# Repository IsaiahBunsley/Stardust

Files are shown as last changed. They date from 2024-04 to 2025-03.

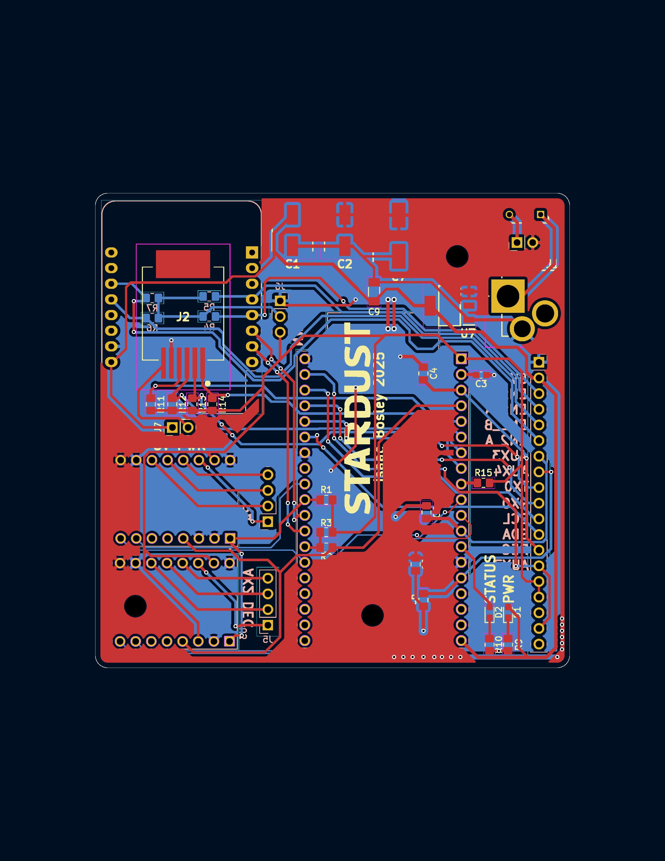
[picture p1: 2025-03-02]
Images/CircuitBoard-page-001 (1).jpg

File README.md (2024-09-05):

# Stardust
Harmonic gear driven equatorial mount for astrophotography.

GOALS:
 - Achieve sub arcsecond prescision
 - Make a sleek and nice-to-view body assembly
 - Use as few pre-made assemblies as possible
 - Ample wieght capacity ( >10 lbs, ideally >20 lbs )
 - Ease of use/control using pre-developed software such as PHD2, OnStep, etc...
 - Design a PCB to house stepper controllers, microcrontroller, WiFi, etc..
 - Efficient homing process
 - Create a product that is not only good-looking but easy to use and enjoy

NOTES:
V1 Is way to large and clunky

Using a 100:1 harmonic and a ~3.33:1 pulley system we can achieve sub arcsecond tracking using 256 microstepping and approx 20 arcsecond tracking with no microstepping. UPDATE: Using a 0.9deg stepper 10 arcsecond (per step)
can be had. A 0.9deg stepper with 1/16 microstepping will give us 0.6 arcseconds per step. This will have to be used to meet design requiremetns as well as to avoid microstepping as it can lead to error.

M3 bolts were used on bolting the body together. If this does not prove to be rigid enough more bolts can be added or a redesign including angle brackets will be needed.

Clearances with the stepper motors are extremely tight. If NEMA 17 motors will not work it would be OK to swap the DEC axis for a smaller NEMA 14 stepper.

Product IDs for the gears are given but expensive. If suitable replacements with similar specs can be found it would be OK to swap. Same with belts. The only issue would be lack of 
quality control from other sources (Amazon...). Cheaping out on a $20 belt would introduce backlash and tracking errors to the ~$1000 harmonic drives.

The angle brackets used to mount the steppers are called out as 6061 alum alloy but could possibly be 3d printed or bought from Mcmaster Carr if a similar design was found.

A redesign of the tangent mount is needed. This tangent mount is made by William Optics and could be fitted into the design for $250: https://williamoptics.com/products/wo-vixen-style-latitude-base-mount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

After looking through the new AM5N's product specs the following seems true:
reduction ratio: 300:1 
         This means that they are using a 100:1 HD paired with a 3:1 belt. With this setup they are claiming a arcsec/step of 0.17. This means that they are using stepper microstepping of 1/64 (0.9 / 300 / 64 = deg -> 0.1687 arcseconds) (also assuming 0.9deg steppers).
There is also a claimed "high payload" mode. I believe that this "mode" simply changes the microstepping value to something more reasonable such as 1/16. This will increase the availiable current per step and thus give more reliable tracking (less periodic error) where more current per step is needed (higher payloads).

DESIGN IDEAS:
For implementing a homing process - Use a arm that mounts to the main axis (axe-eees) that goes down the length of the HD and will pass over some sort of magnetic sensor or inductive position
sensor. This will allow the motors to spin the HD until a sensor detects an object meaning the output shaft of the HD is in the correct location.

Add an encoder and brake to the stepper shaft. 

Allow for EQ mode OR an alt/az mode (by removing the tangent assembly).

INSPIRATION:
Alkaid by JZ - https://github.com/alanzjl/AlkaidMount
ZWO AM5 - https://www.highpointscientific.com/zwo-am5n-harmonic-drive-equatorial-mount-with-tripod
William Optics Latitude Base - https://williamoptics.com/products/wo-vixen-style-latitude-base-mount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

0.9 Stepper - https://www.moonsindustries.com/p/nema-17-high-precision-hybrid-stepper-motors/ms17ha4p4040-000004611110015909
ONSTEP      - https://onstep.groups.io/g/main/wiki/4414

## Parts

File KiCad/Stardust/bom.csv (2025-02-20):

Id | Designator | Footprint | Quantity | Designation | Supplier and ref
1 | C6,C5,C8,C4 | C_2220_5750Metric_Pad1.97x5.40mm_HandSolder | 4 | 100nF
2 | R1,R3,R9,R10,R6,R5,R4,R7 | R_0805_2012Metric_Pad1.20x1.40mm_HandSolder | 8 | 4.7K
3 | D2 | LED_0603_1608Metric_Pad1.05x0.95mm_HandSolder | 1 | STATUS LED
4 | J7,J3 | PinHeader_1x02_P2.54mm_Vertical | 2 | 1x2 Connector
5 | J2 | RJ12_855135114 | 1 | RJ12
6 | R14,R15,R13,R12,R11 | R_0805_2012Metric_Pad1.20x1.40mm_HandSolder | 5 | 2.4K
7 | U8 | FuseHolder_RHDR2W53P0X508_1X2 | 1 | LittlFuse 2.5 Amp
8 | G1,G1 | logo_footprint | 2 | LOGO
9 | C7 | 100uFElectrolyticCap_CAPAE830X1080N | 1 | 100 uF
10 | U7 | 5VREG_SOT230P700X180-4N | 1 | Regulator - 5V 1A
11 | C2,C1 | 10uFElectrolyticCap_CAPAE660X550N | 2 | 10 uF
12 | D1 | LED_0603_1608Metric_Pad1.05x0.95mm_HandSolder | 1 | PWR LED
13 | C3 | C_0603_1608Metric_Pad1.08x0.95mm_HandSolder | 1 | 10uF
14 | C9 | C_1206_3216Metric_Pad1.33x1.80mm_HandSolder | 1 | 330nF
15 | R2 | R_0805_2012Metric_Pad1.20x1.40mm_HandSolder | 1 | 1K
16 | J1 | DC_PowerConn_694108402002 | 1 | 12V DC
17 | U2,U3 | MODULE_TMC2209_SILENTSTEPSTICK | 2 | BTT TMC2209 V1.3
18 | U1 | MODULE_ESP32-DEVKITC | 1 | ESP32
19 | J5,J4 | PinHeader_1x04_P2.54mm_Vertical | 2 | Conn_01x04_Pin
20 | J6 | PinHeader_1x03_P2.54mm_Vertical | 1 | 1x3 Header
21 | J8 | PinHeader_1x19_P2.54mm_Vertical | 1 | Conn_01x19_Pin
22 | U4 | WEMOS_D1_mini_light | 1 | WEMOS_D1_mini

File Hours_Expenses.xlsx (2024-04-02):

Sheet: Hours
Date | Hours | Total Days | Total Hours
2024-03-21 | 8 | 0.50 | 12
2024-03-22 | 4

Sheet: Expenses
Item | Cost per Item | Shipping | Taxes | Quantity | Total | Total Spent
CSF-17-100-2UH Harmonic Drive | $210.00 | $8.00 | $28.89 | 2 | $456.89 | $456.89

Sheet: Sheet1
Part Number | Item Name | Manufacturer | Cost | Comment
60-2P06MDFP8 | GT2 Timing Belt Pulley 18 Tooth | B&B Manufacturing | $18.20 | B&B Items do not have CAD files so cannot test fitment
GPA18GT2060-A-H5 | GT2 Timing Belt Pulley 18 Tooth | MISUMI | $18.10
18-2P06M6FA5 | GT2 Timing Belt Pulley 60 Tooth | B&B Manufacturing | $7.63 | B&B Items do not have CAD files so cannot test fitment
GPA60GT2060-A-H8 | GT2 Timing Belt Pulley 60 Tooth | MISUMI | $28.32
144-2P-06 | GT2 Belt 144mm | B&B Manufacturing | $6.34 | B&B Items do not have CAD files so cannot test fitment
GBN1442GT-60 | GT2 Belt 144mm | MISUMI | $6.50
DW-AD-601-M8-121 | Inductive Position Sensor | Contrinex | $17.00
59060-1-T-03-A | Inductive Position Sensor | Littelfuse | $9.83
 |  |  | $64.46

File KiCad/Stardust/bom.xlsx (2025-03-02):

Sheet: bom
Mouser/DigiKey PN | MFR PN | Quantity | Price | Total | Mouser | Digikey | Amazon | Ordered?
710-865230643009 | 865230643009 | 2 | $0.26 | $0.52 | y |  |  | y
810-C1608X7T1A106M08 | C1608X7T1A106M080AC | 1 | $0.23 | $0.23 | y |  |  | y
581-KAM21BR71H104JT | KAM21BR71H104JT | 4 | $0.32 | $1.28 | y |  |  | y
647-GXC1V101MCQ1GS | GXC1V101MCQ1GS | 1 | $1.78 | $1.78 | y |  |  | y
581-KAM31NR81H334KU | KAM31NR81H334KU | 1 | $0.49 | $0.49 | y |  |  | y
720-P4112S2U1252X4X5 | KT EELP41.12-S2U1-25-2X4X-5-R18 | 2 | $0.30 | $0.60 | y |  |  | y
710-694108402002 | 694108402002 | 1 | $1.21 | $1.21 | y |  |  | y
538-85513-5002 | 85513-5002 | 1 | $0.97 | $0.97 | y |  |  | y
667-ERA-6VEB4701V | ERA-6VEB4701V | 8 | $0.40 | $3.20 | y |  |  | y
754-RS2012P-102-DT53 | RS2012P-102-D-T5-3 | 1 | $0.46 | $0.46 | y |  |  | y
754-RG2012P-242-B-T5 | RG2012P-242-B-T5 | 5 | $0.21 | $1.05 | y |  |  | y
1965-ESP32-DEVKITC-32UE-ND | ESP32-DEVKITC-32UE | 1 | $10.00 | $10.00 |  |  | y | y
3647-26225-ND | 26225 | 1 | $4.81 | $4.81 |  |  | y | y
821-TS1117BCW50RPG | TS1117BCW50 RPG | 1 | $0.75 | $0.75 | y |  |  | y
576-56200001009 | 56200001009 | 1 | $1.32 | $1.32 | y |  |  | y
TMC2209 Steppers | amazon (https://www.amazon.com/BIGTREETECH-DIRECT-TMC2209-Stepsticks-Motherboard/dp/B07ZPYKL46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) | 1 | $22.99 | $22.99 |  |  | y | y
 |  |  |  | $51.66

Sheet: items
Designator | Mouser/DigiKey PN | MFR PN
C1 | 710-865230643009 | 865230643009
C2 | 710-865230643009 | 865230643009
C3 | 810-C1608X7T1A106M08 | C1608X7T1A106M080AC
C4 | 581-KAM21BR71H104JT | KAM21BR71H104JT
C5 | 581-KAM21BR71H104JT | KAM21BR71H104JT
C6 | 581-KAM21BR71H104JT | KAM21BR71H104JT
C7 | 647-GXC1V101MCQ1GS | GXC1V101MCQ1GS
C8 | 581-KAM21BR71H104JT | KAM21BR71H104JT
C9 | 581-KAM31NR81H334KU | KAM31NR81H334KU
D1 | 720-P4112S2U1252X4X5 | KT EELP41.12-S2U1-25-2X4X-5-R18
D2 | 720-P4112S2U1252X4X5 | KT EELP41.12-S2U1-25-2X4X-5-R18
J1 | 710-694108402002 | 694108402002
J2 | 538-85513-5002 | 85513-5002
R1 | 667-ERA-6VEB4701V | ERA-6VEB4701V
R2 | 754-RS2012P-102-DT53 | RS2012P-102-D-T5-3
R3 | 667-ERA-6VEB4701V | ERA-6VEB4701V
R4 | 667-ERA-6VEB4701V | ERA-6VEB4701V
R5 | 667-ERA-6VEB4701V | ERA-6VEB4701V
R6 | 667-ERA-6VEB4701V | ERA-6VEB4701V
R7 | 667-ERA-6VEB4701V | ERA-6VEB4701V
R9 | 667-ERA-6VEB4701V | ERA-6VEB4701V
R10 | 667-ERA-6VEB4701V | ERA-6VEB4701V
R11 | 754-RG2012P-242-B-T5 | RG2012P-242-B-T5
R12 | 754-RG2012P-242-B-T6 | RG2012P-242-B-T6
R13 | 754-RG2012P-242-B-T7 | RG2012P-242-B-T7
R14 | 754-RG2012P-242-B-T8 | RG2012P-242-B-T8
R15 | 754-RG2012P-242-B-T9 | RG2012P-242-B-T9
U1 | 1965-ESP32-DEVKITC-32UE-ND | ESP32-DEVKITC-32UE
U2
U3
U4 | 3647-26225-ND | 26225
U7 | 821-TS1117BCW50RPG | TS1117BCW50 RPG
U8 | 576-56200001009 | 56200001009

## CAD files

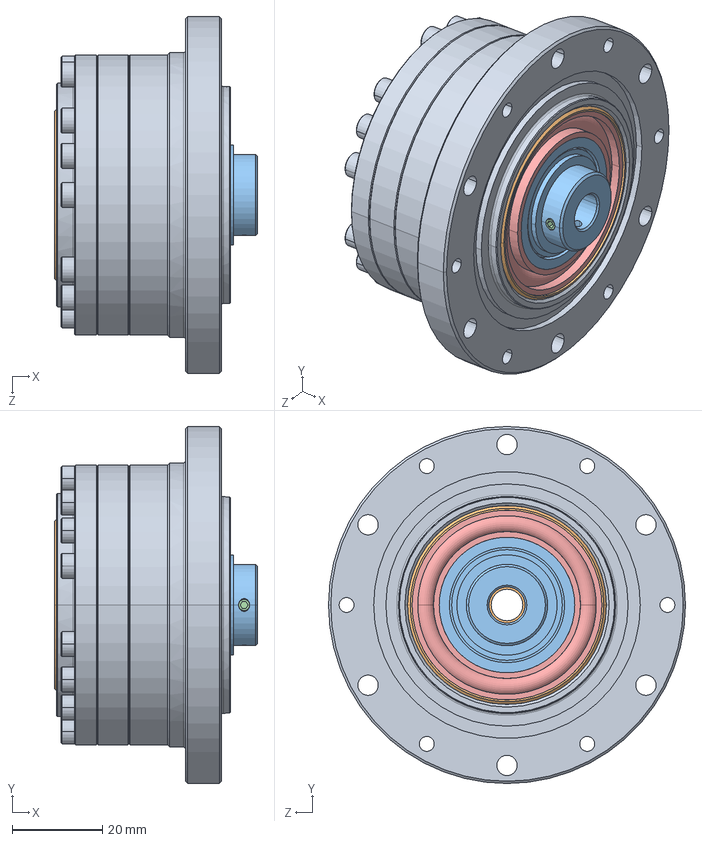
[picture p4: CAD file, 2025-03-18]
Components/csf-17-xxx-2uh.SLDASM
45.0 x 79.0 x 79.0 mm
CSF-17-2UH HOUSING.stp
CSF-17-2UH OUTPUT.stp
CSF-17-2A-R OLDHAM COUPLING.stp
1715063_1715063.stp x 2
17 WG BEARING.stp

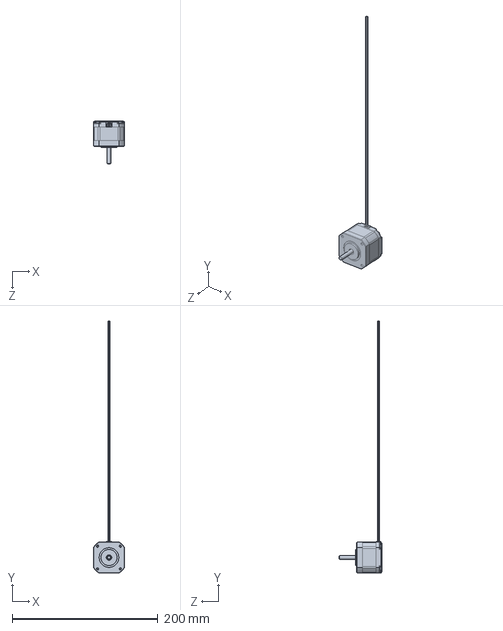
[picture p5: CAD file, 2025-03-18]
Components/STEPPER_2.3.SLDPRT
42.4 x 345.4 x 58.3 mm

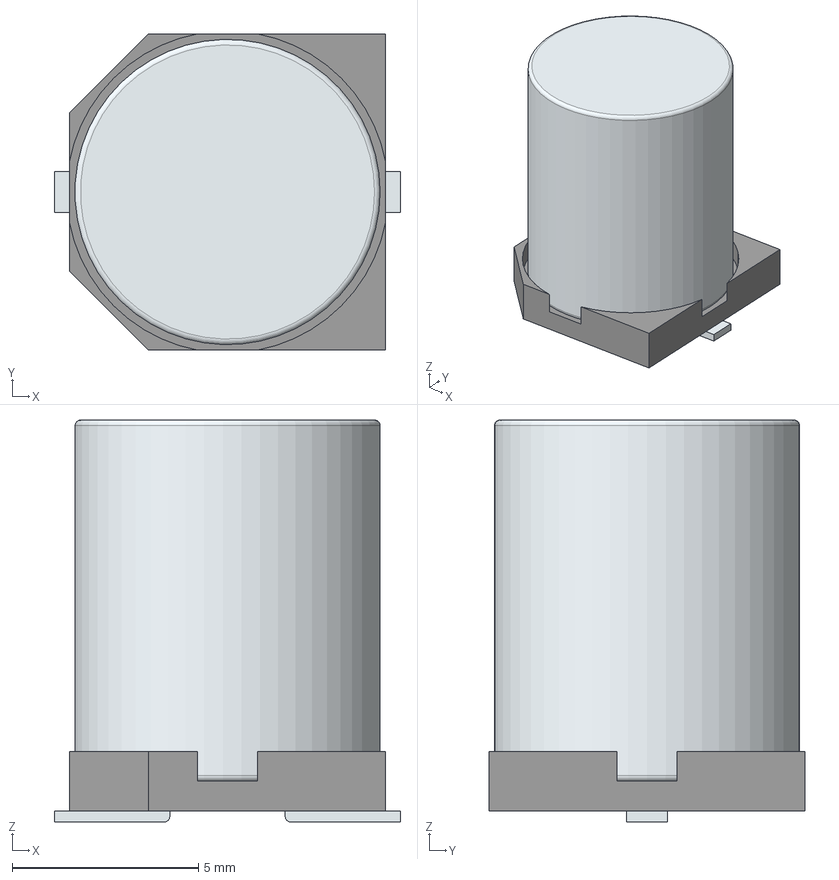
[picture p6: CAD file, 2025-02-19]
KiCad/Stardust/3d_models/100uFElectrolyticCap_GXC1V101MCQ1GS.stp
9.30 x 8.50 x 10.8 mm
Base
Pin1Fillet
Pin2Fillet

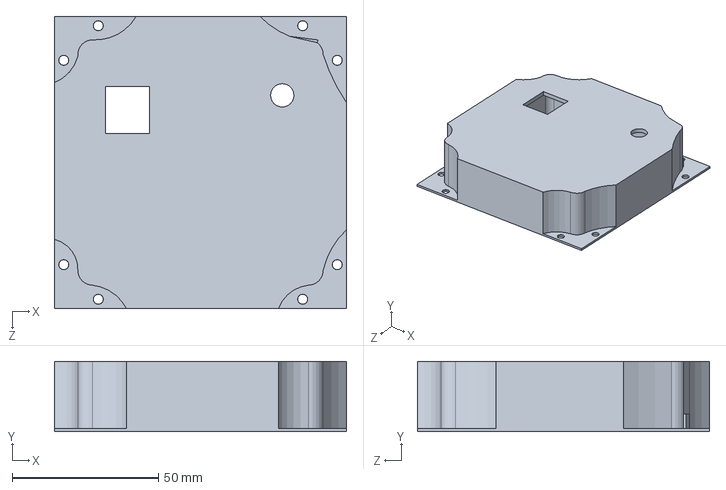
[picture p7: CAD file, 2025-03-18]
Stardust V2/STARDUST_COMPUTERMOUNT_PART2_V2.SLDPRT
100.0 x 24.0 x 100.0 mm

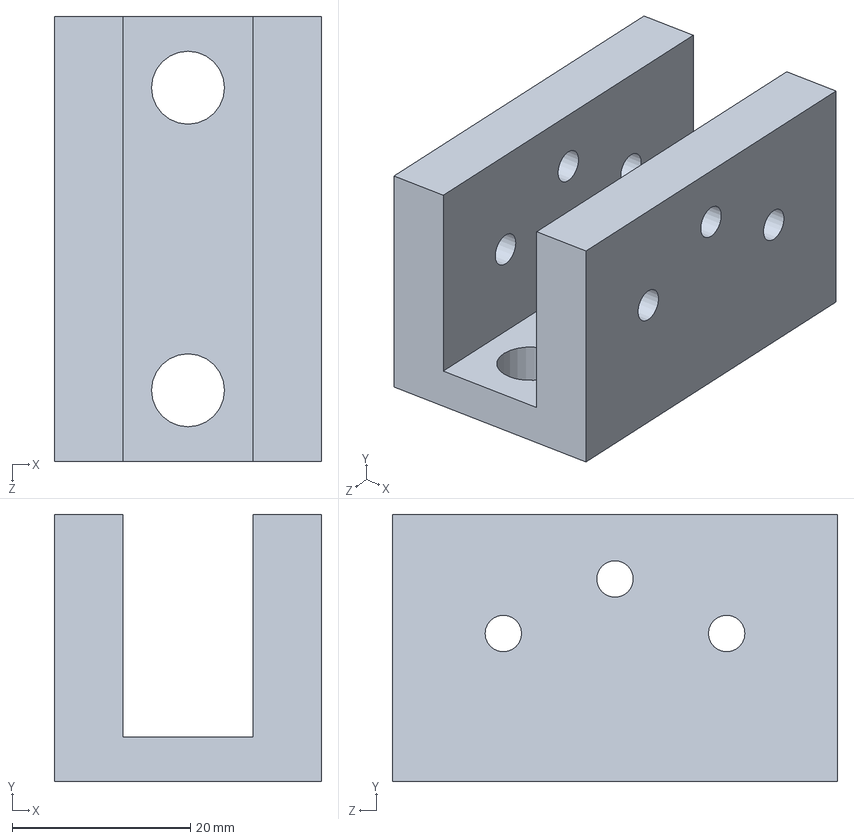
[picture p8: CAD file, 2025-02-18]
Temp/latitude base connector FEMALE.SLDPRT
30.0 x 30.0 x 50.0 mm

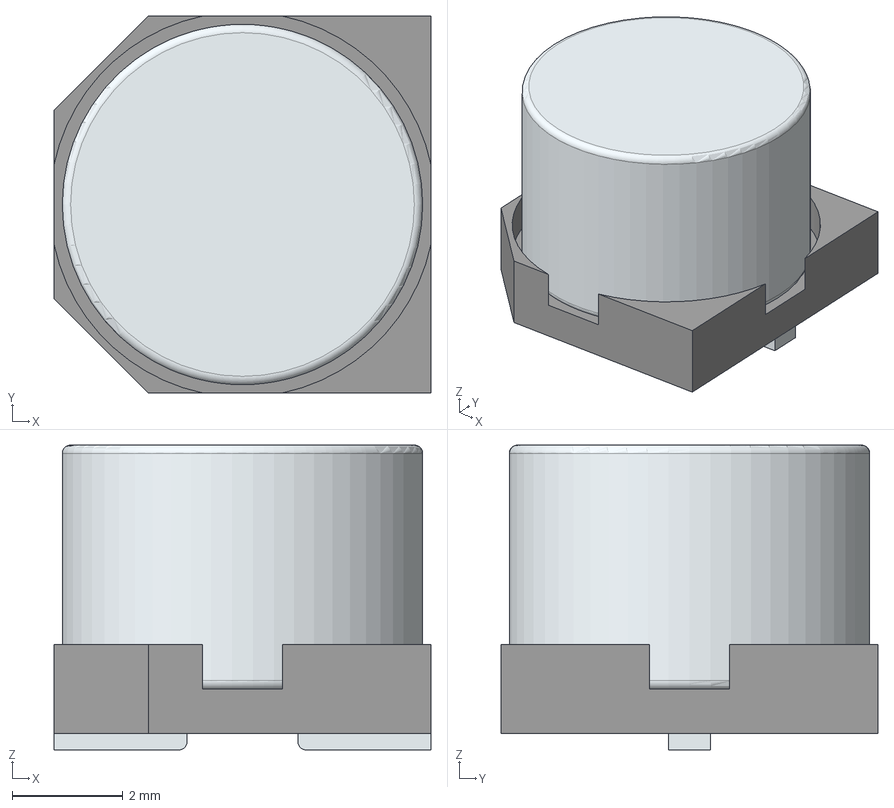
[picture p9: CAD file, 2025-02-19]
KiCad/Stardust/3d_models/10uFElectrolyticCap_865230643009.stp
6.80 x 6.80 x 5.50 mm
Base
Pin1Fillet
Pin2Fillet

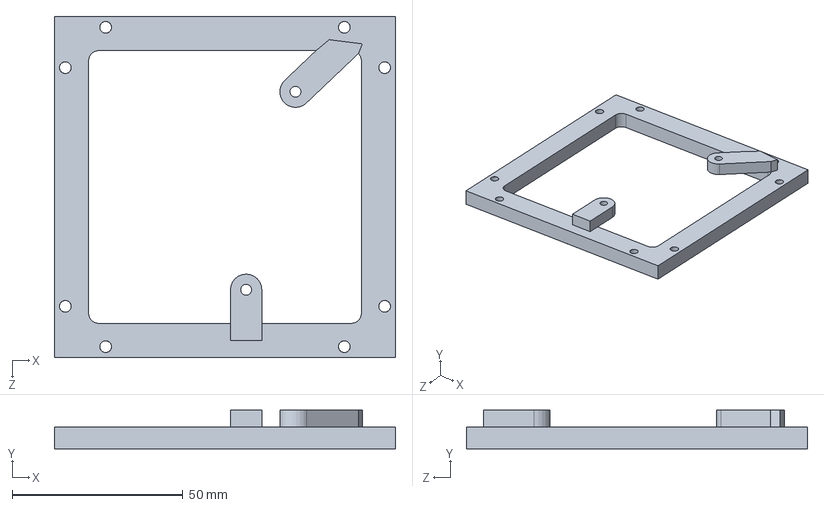
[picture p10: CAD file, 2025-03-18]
Stardust V2/STARDUST_COMPUTERMOUNT_V2.SLDPRT
100.0 x 11.4 x 100.0 mm

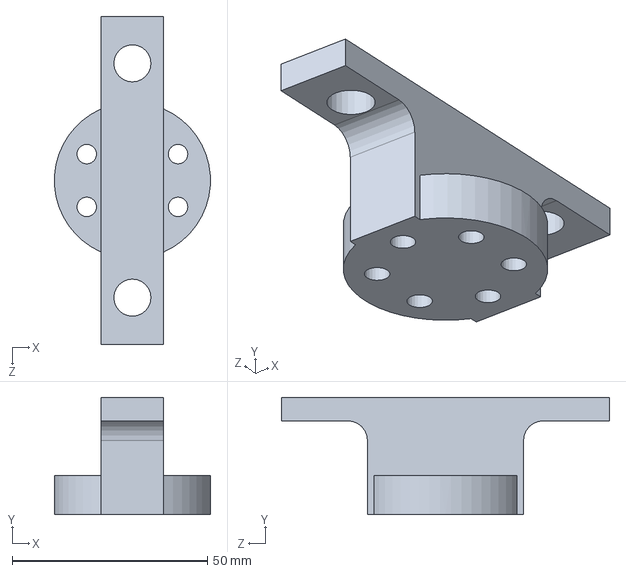
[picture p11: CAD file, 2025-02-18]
Temp/HD_TO_ORIONSTRADDLE.SLDPRT
40.0 x 30.0 x 84.0 mm

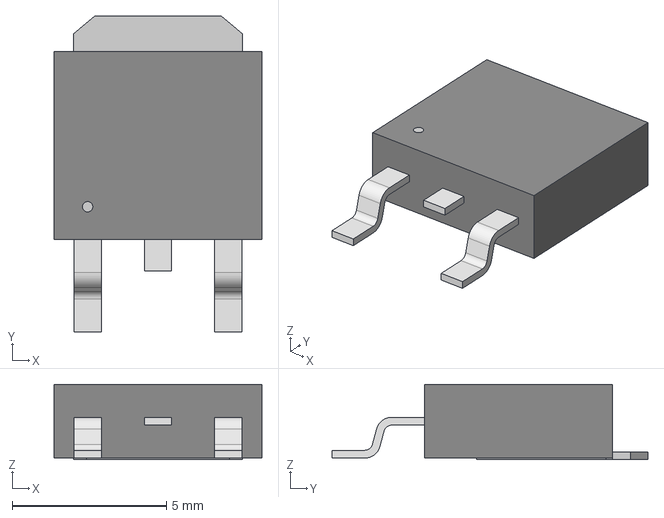
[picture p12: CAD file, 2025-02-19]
KiCad/Stardust/3d_models/12VREG_TO-252-3-L1_NMD.step
6.73 x 10.2 x 2.44 mm

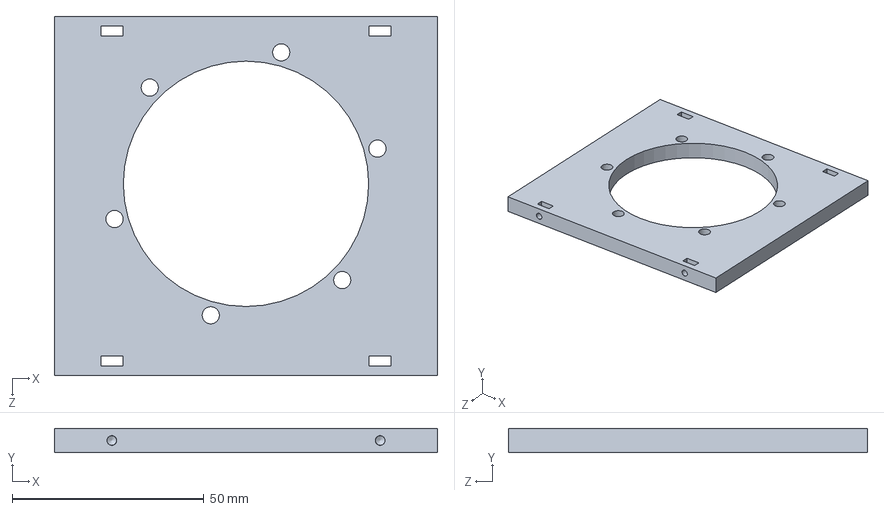
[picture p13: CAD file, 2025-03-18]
Stardust V2/STARDUST_DEC_HARMONICMOUNT_V2.SLDPRT
100.0 x 6.35 x 93.7 mm

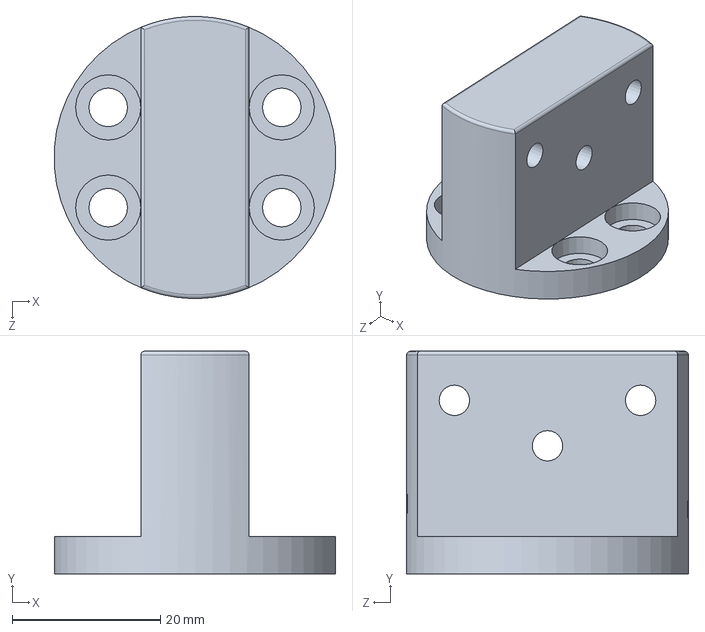
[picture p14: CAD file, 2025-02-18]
Temp/latitude base connector MALE.SLDPRT
37.9 x 30.0 x 38.0 mm

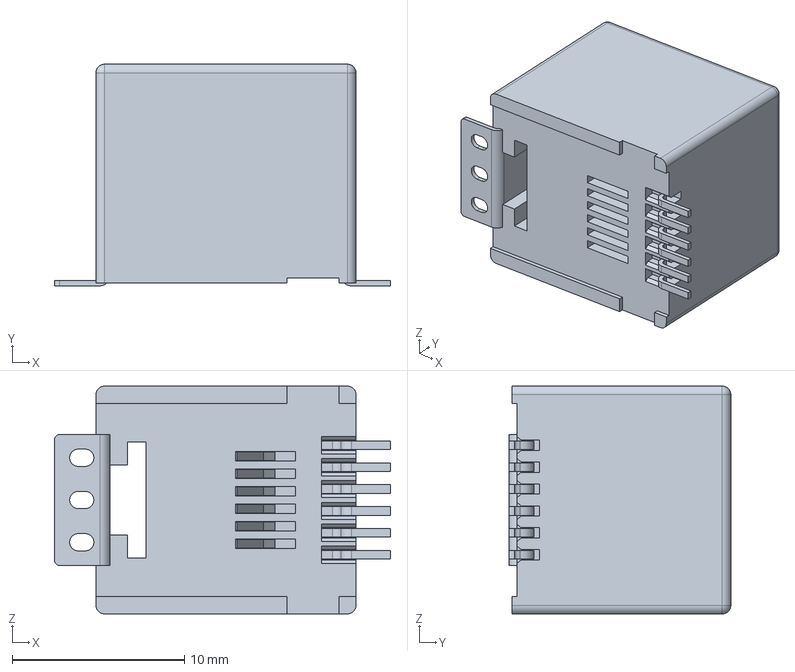
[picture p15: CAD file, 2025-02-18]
KiCad/Stardust/3d_models/RJ12_85513-5002.stp
19.5 x 12.8 x 13.2 mm

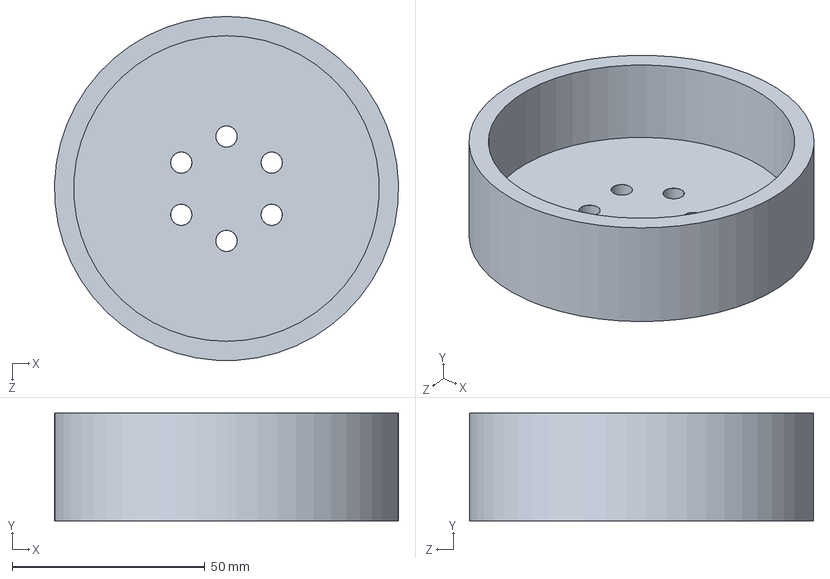
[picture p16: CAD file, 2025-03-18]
Stardust V2/STARDUST_DEC_HDCOVER.SLDPRT
89.3 x 28.0 x 89.3 mm

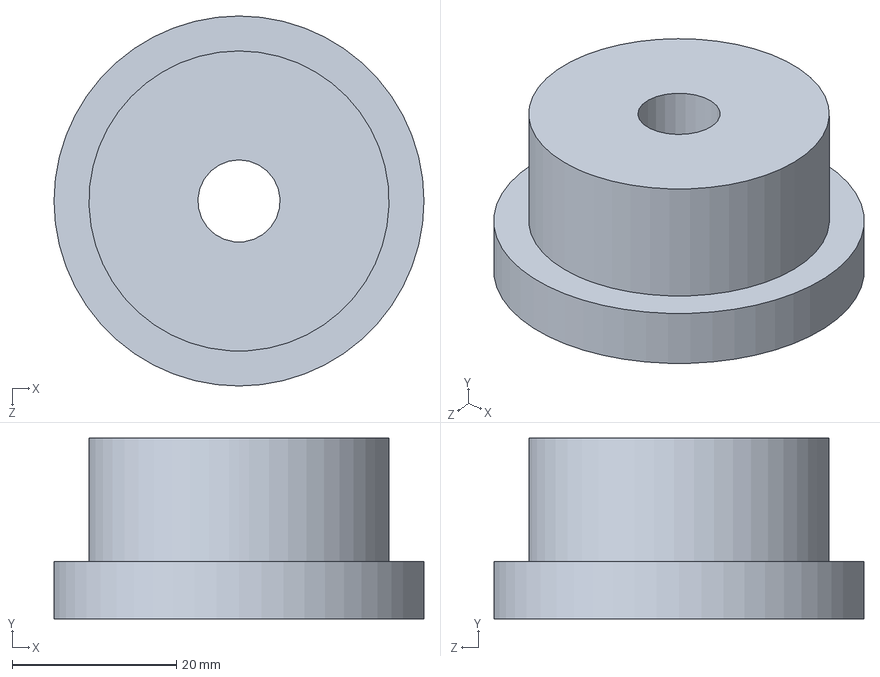
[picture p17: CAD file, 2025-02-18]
Temp/orion mount bracket.SLDPRT
45.0 x 22.0 x 45.0 mm

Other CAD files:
Stardust V2/STARDUST_V2.SLDASM
Components/GPA60GT2060-A-H8_b.sldprt
Components/GPA18GT2060-A-H5_b.sldprt
Components/STEPPER_2.5.SLDPRT
Components/M4x14_BOLT.SLDPRT
KiCad/Stardust/3d_models/12VREG_DPAK-3_ONS.step
KiCad/Stardust/3d_models/5188 DS3231 RTC.step
KiCad/Stardust/3d_models/5VREG_TS1117BCW50_RPG.stp
KiCad/Stardust/3d_models/DC_Power_Connector.stp
KiCad/Stardust/3d_models/FuseHolder_RHDR2W53P0X508_1X2.stp
KiCad/Stardust/3d_models/SDIODE_SS310BF-HF.stp
KiCad/Stardust/3d_models/TMC2209_SILENTSTEPSTICK.step
KiCad/Stardust/3d_models/d1miniv3.stl
Stardust V1/STARDUST.SLDASM
Stardust V1/STARDUST_DECHARMONICMOUNT_V1.SLDPRT
Stardust V1/STARDUST_DEC_AXIS.SLDASM
Stardust V1/STARDUST_L_BRACKET.SLDPRT
Stardust V1/STARDUST_RAHARMONICMOUNT_V1.SLDPRT
Stardust V1/STARDUST_RA_AXIS.SLDASM
Stardust V1/STARDUST_STEPPER_BRACKET_V1.SLDPRT
Stardust V2/3mf/STARDUST_COMPUTERMOUNT_PART2_V2.3MF
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

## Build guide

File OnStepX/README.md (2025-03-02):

OnStepX Telescope Controller
===========================

# What is OnStepX?
OnStepX is the advanced version of the OnStep computerized telescope controller with support for interfacing with/controlling a variety of motor drivers (and so motors) including Step/Dir, ODrive, and Servo (a combination of encoder and DC motor or Stepper motor) types.

It supports:
* Telescope Mount control (Alt/Azm and Equatorial GEM/Fork.)  Optional support for Eq mounts with Tangent Arm Declination.  Usually the Goto capability is enabled, but that's optional as well for those who just want basic mount control.
* Telescope Rotator control (including Alt/Azm de-rotation.)
* Telescope Focuser control (up to 6 focusers so it can handle collimation as well as focusing.)
* Telescope Accessory control (combination of up to 8 dew-heaters, switches, analog PWM.)

# Features
OnStepX supports a wide variety of connection options.  Several serial
"command channels" can be utilized. One of the these is normally devoted to a USB
connection and for the other(s) choose from the following:

* Bluetooth
* ESP8266 WiFi
* Arduino M0/Ethernet Shield
* Even another USB port or RS232 serial isn't very difficult to add.

In the case of running OnStepX on an ESP32 it can provide its own Bluetooth or WiFi IP command channels without additional hardware by simply activating the feature in OnStepX.

Other software in the OnStep ecosystem include:

* an [ASCOM](http://ascom-standards.org/) driver (with IP and Serial support),
* an Android App useable over WiFi or Bluetooth equipped Phones/Tablets,
* a "built-in" website (on the Ethernet and/or WiFi device),
* a full planetarium program that controls all features ([Sky Planetarium](http://stellarjourney.com/index.php?r=site/software_sky)).

OnStep is compatible with the LX200 protocol. This means it can be controlled
from other planetarium software, like: Sky Safari, CdC (even without ASCOM),
Stellarium, etc.

There are also [INDI](http://www.indilib.org/about.html) drivers so it can be used from Linux, with CdC or KStars.

# Documentation
Detailed documentation, including the full set of features, detailed designs for
PCBs, instructions on how to build a controller, how to configure the firmware
for your particular mount, can all be found the [OnStep Group Wiki](https://groups.io/g/onstep/wiki/home).

# Change Log
All the changes are tracking in git, and a detailed list can be accessed using the
following git command:
 
git log --date=short --pretty=format:"%h %ad %<(20)%an %<(150,trunc)%s"

# Support
Questions and discussion should be on the mailing list (also accessible via the
web) at the [OnStep Group](https://groups.io/g/onstep/).

# License
OnStep is open source free software, licensed under the GPL.

See [LICENSE.txt](./LICENSE.txt) file.

# Author
[Howard Dutton](http://www.stellarjourney.com)

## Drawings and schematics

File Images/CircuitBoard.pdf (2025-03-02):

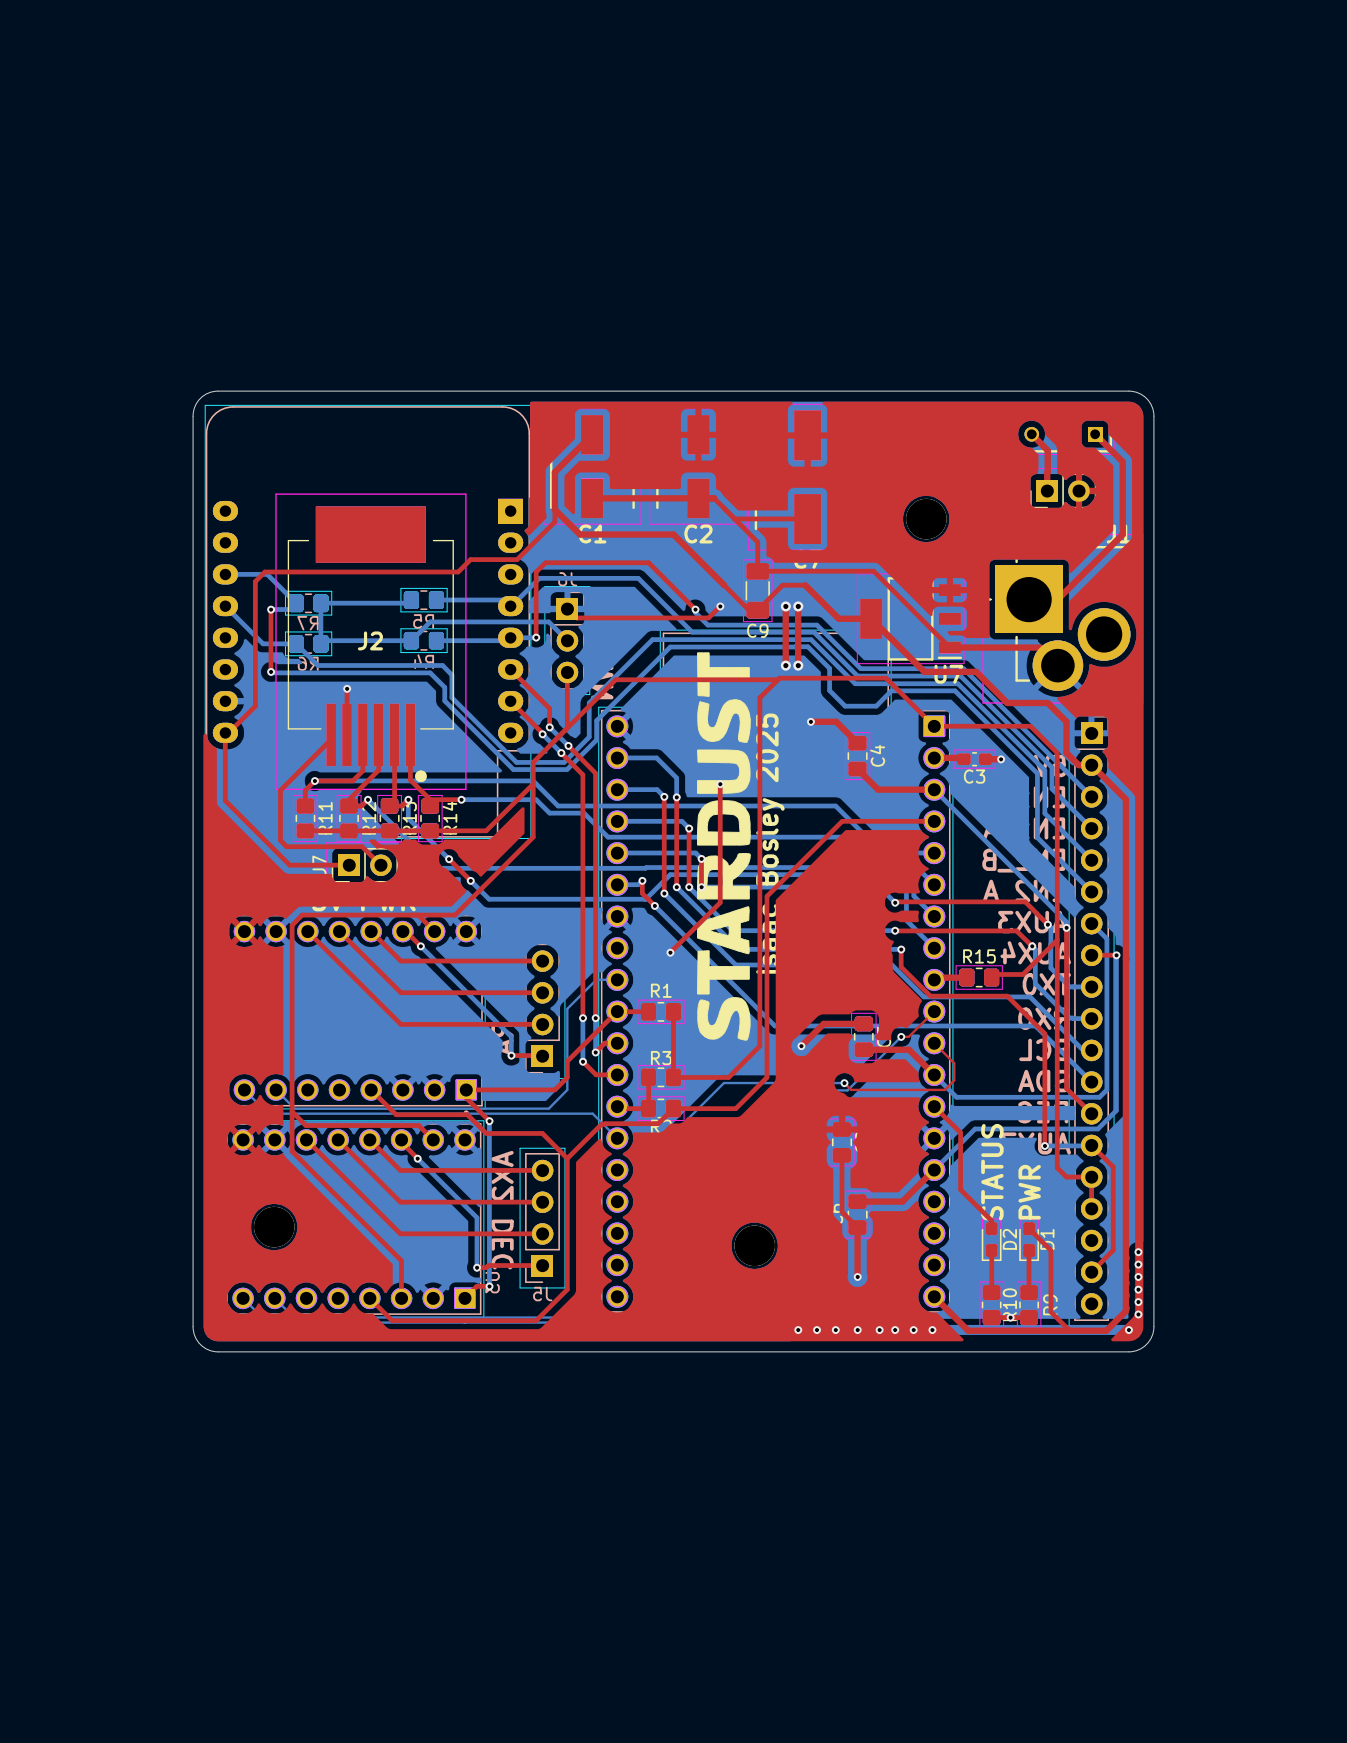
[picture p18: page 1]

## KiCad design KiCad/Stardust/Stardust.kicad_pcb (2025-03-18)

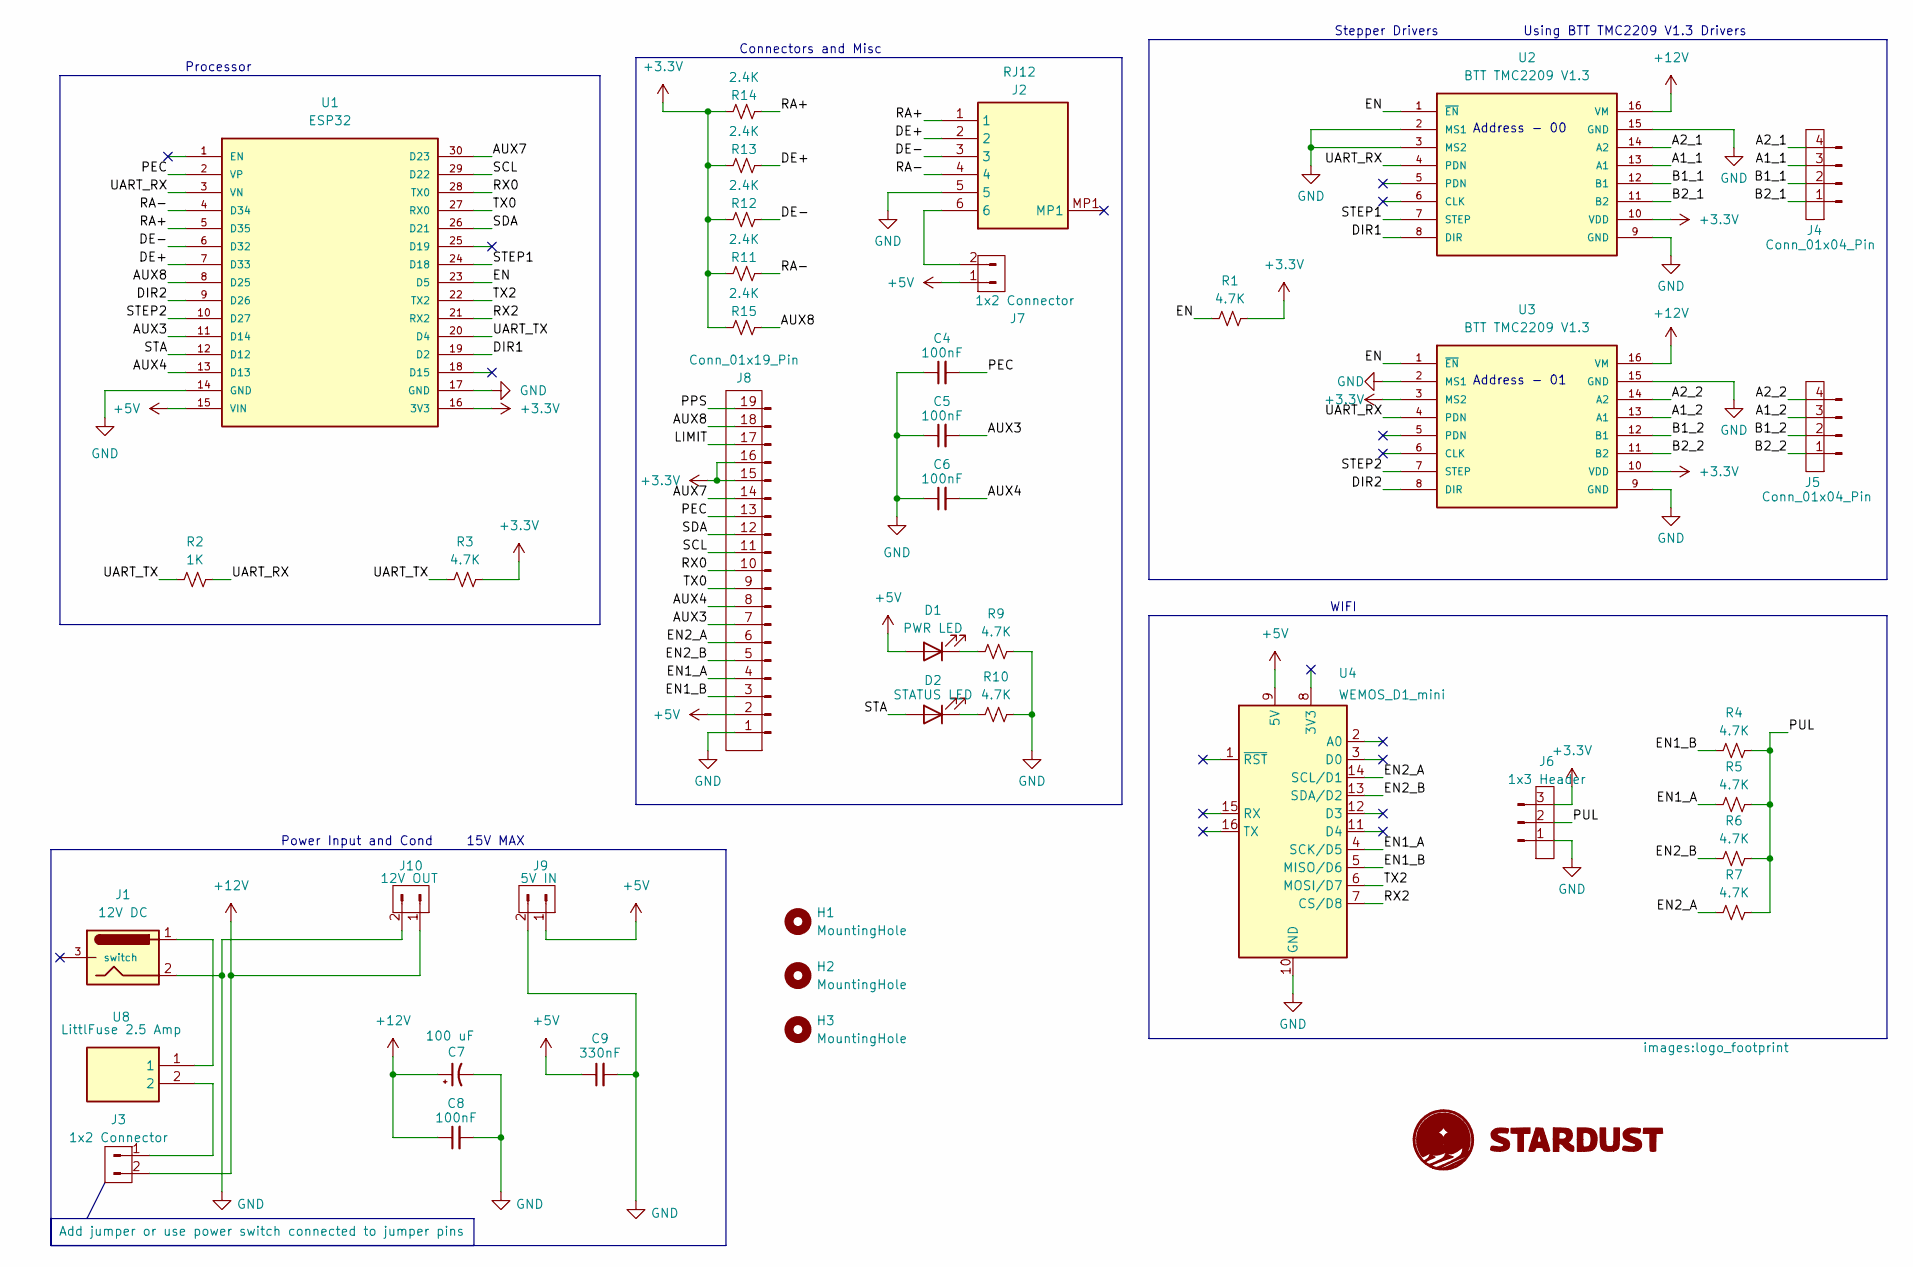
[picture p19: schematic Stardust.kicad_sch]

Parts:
C4, C5, C6, C8: 100nF; C_0805_2012Metric_Pad1.18x1.45mm_HandSolder; Mouser PN 581-KAM21BR71H104JT
C7: 100 uF; 100uFElectrolyticCap_CAPAE830X1080N; Mouser PN 647-GXC1V101MCQ1GS
C9: 330nF; C_1206_3216Metric_Pad1.33x1.80mm_HandSolder; Mouser PN 581-KAM31NR81H334KU
D1: PWR LED; LED_0603_1608Metric_Pad1.05x0.95mm_HandSolder
D2: STATUS LED; LED_0603_1608Metric_Pad1.05x0.95mm_HandSolder
G1: LOGO; logo_footprint
H1, H2, H3: MountingHole; MountingHole_3.2mm_M3
J1: 12V DC; DC_PowerConn_694108402002
J2: RJ12; RJ12_855135114; Mouser Part Number 538-85513-5002
J3, J7: 1x2 Connector; PinHeader_1x02_P2.54mm_Vertical
J4, J5: Conn_01x04_Pin; PinHeader_1x04_P2.54mm_Vertical
J6: 1x3 Header; PinHeader_1x03_P2.54mm_Vertical
J8: Conn_01x19_Pin; PinHeader_1x19_P2.54mm_Vertical
J9: 5V IN; PinHeader_1x02_P2.54mm_Vertical
J10: 12V OUT; PinHeader_1x02_P2.54mm_Vertical
R1, R3, R4, R5, R6, R7, R9, R10: 4.7K; R_0805_2012Metric_Pad1.20x1.40mm_HandSolder
R2: 1K; R_0805_2012Metric_Pad1.20x1.40mm_HandSolder
R11, R12, R13, R14, R15: 2.4K; R_0805_2012Metric_Pad1.20x1.40mm_HandSolder
U1: ESP32; MODULE_ESP32-DEVKITC
U2, U3: BTT TMC2209 V1.3; MODULE_TMC2209_SILENTSTEPSTICK
U4: WEMOS_D1_mini; WEMOS_D1_mini_light
U8: LittlFuse 2.5 Amp; FuseHolder_RHDR2W53P0X508_1X2; Mouser Part Number 576-56200001009

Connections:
+3.3V: J6.3, J8.15, J8.16, R1.2, R3.2, R11.2, R12.2, R13.2, R14.2, R15.2, U1.16 (3V3), U2.10 (VDD), U3.3 (MS2), U3.10 (VDD)
+5V: C9.1, D1.2 (A), J7.1, J8.2, J9.1, U1.15 (VIN), U4.9 (5V)
+12V: C7.1, C8.1, J3.2, J10.1, U2.16 (VM), U3.16 (VM)
/A1_1: J4.3, U2.13 (A1)
/A1_2: J5.3, U3.13 (A1)
/A2_1: J4.4, U2.14 (A2)
/A2_2: J5.4, U3.14 (A2)
/AUX3: C5.2, J8.7, U1.11 (D14)
/AUX4: C6.2, J8.8, U1.13 (D13)
/AUX7: J8.14, U1.30 (D23)
/AUX8: J8.18, R15.1, U1.8 (D25)
/B1_1: J4.2, U2.12 (B1)
/B1_2: J5.2, U3.12 (B1)
/B2_1: J4.1, U2.11 (B2)
/B2_2: J5.1, U3.11 (B2)
/DE+: J2.2, R13.1, U1.7 (D33)
/DE-: J2.3, R12.1, U1.6 (D32)
/DIR1: U1.19 (D2), U2.8 (DIR)
/DIR2: U1.9 (D26), U3.8 (DIR)
/EN: R1.1, U1.23 (D5), U2.1 (~EN), U3.1 (~EN)
/EN1_A: J8.4, R5.1, U4.4 (SCK/D5)
/EN1_B: J8.3, R4.1, U4.5 (MISO/D6)
/EN2_A: J8.6, R7.1, U4.14 (SCL/D1)
/EN2_B: J8.5, R6.1, U4.13 (SDA/D2)
/LIMIT: J8.17
/PEC: C4.2, J8.13, U1.2 (VP)
/PPS: J8.19
/PUL: J6.2, R4.2, R5.2, R6.2, R7.2
/RA+: J2.1, R14.1, U1.5 (D35)
/RA-: J2.4, R11.1, U1.4 (D34)
/RX0: J8.10, U1.28 (TX0)
/RX2: U1.21 (RX2), U4.7 (CS/D8)
/SCL: J8.11, U1.29 (D22)
/SDA: J8.12, U1.26 (D21)
/STA: D2.2 (A), U1.12 (D12)
/STEP1: U1.24 (D18), U2.7 (STEP)
/STEP2: U1.10 (D27), U3.7 (STEP)
/TX0: J8.9, U1.27 (RX0)
/TX2: U1.22 (TX2), U4.6 (MOSI/D7)
/UART_RX: R2.2, U1.3 (VN), U2.4 (PDN), U3.4 (PDN)
/UART_TX: R2.1, R3.1, U1.20 (D4)
GND: C4.1, C5.1, C6.1, C7.2, C8.2, C9.2, J1.2, J2.5, J6.1, J8.1, J9.2, J10.2, R9.2, R10.2, U1.14 (GND), U1.17 (GND), U2.2 (MS1), U2.3 (MS2), U2.9 (GND), U2.15 (GND), U3.2 (MS1), U3.9 (GND), U3.15 (GND), U4.10 (GND)
unnamed: D1.1 (K), R9.1
unnamed: D2.1 (K), R10.1
unnamed: J1.1, U8.1
unnamed: J3.1, U8.2
unnamed: J2.6, J7.2

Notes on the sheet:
Processor
Connectors and Misc
Using BTT TMC2209 V1.3 Drivers
WIFI
15V MAX
Stepper Drivers
Address - 01
Power Input and Cond
Address - 00

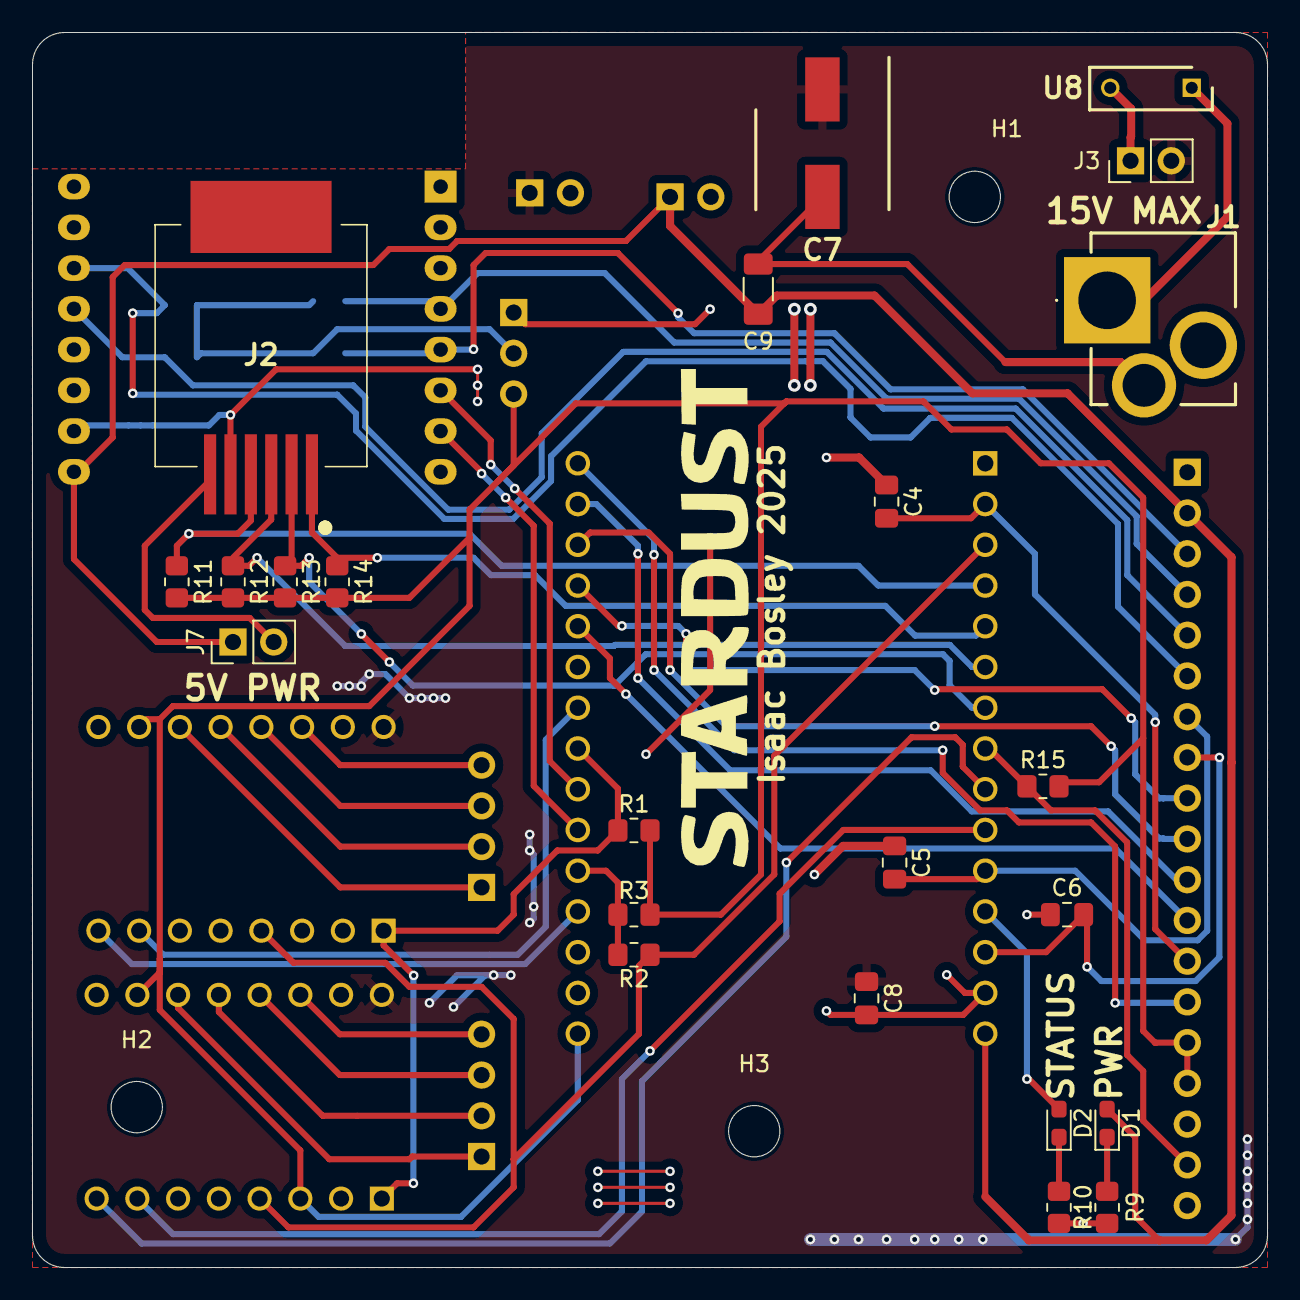
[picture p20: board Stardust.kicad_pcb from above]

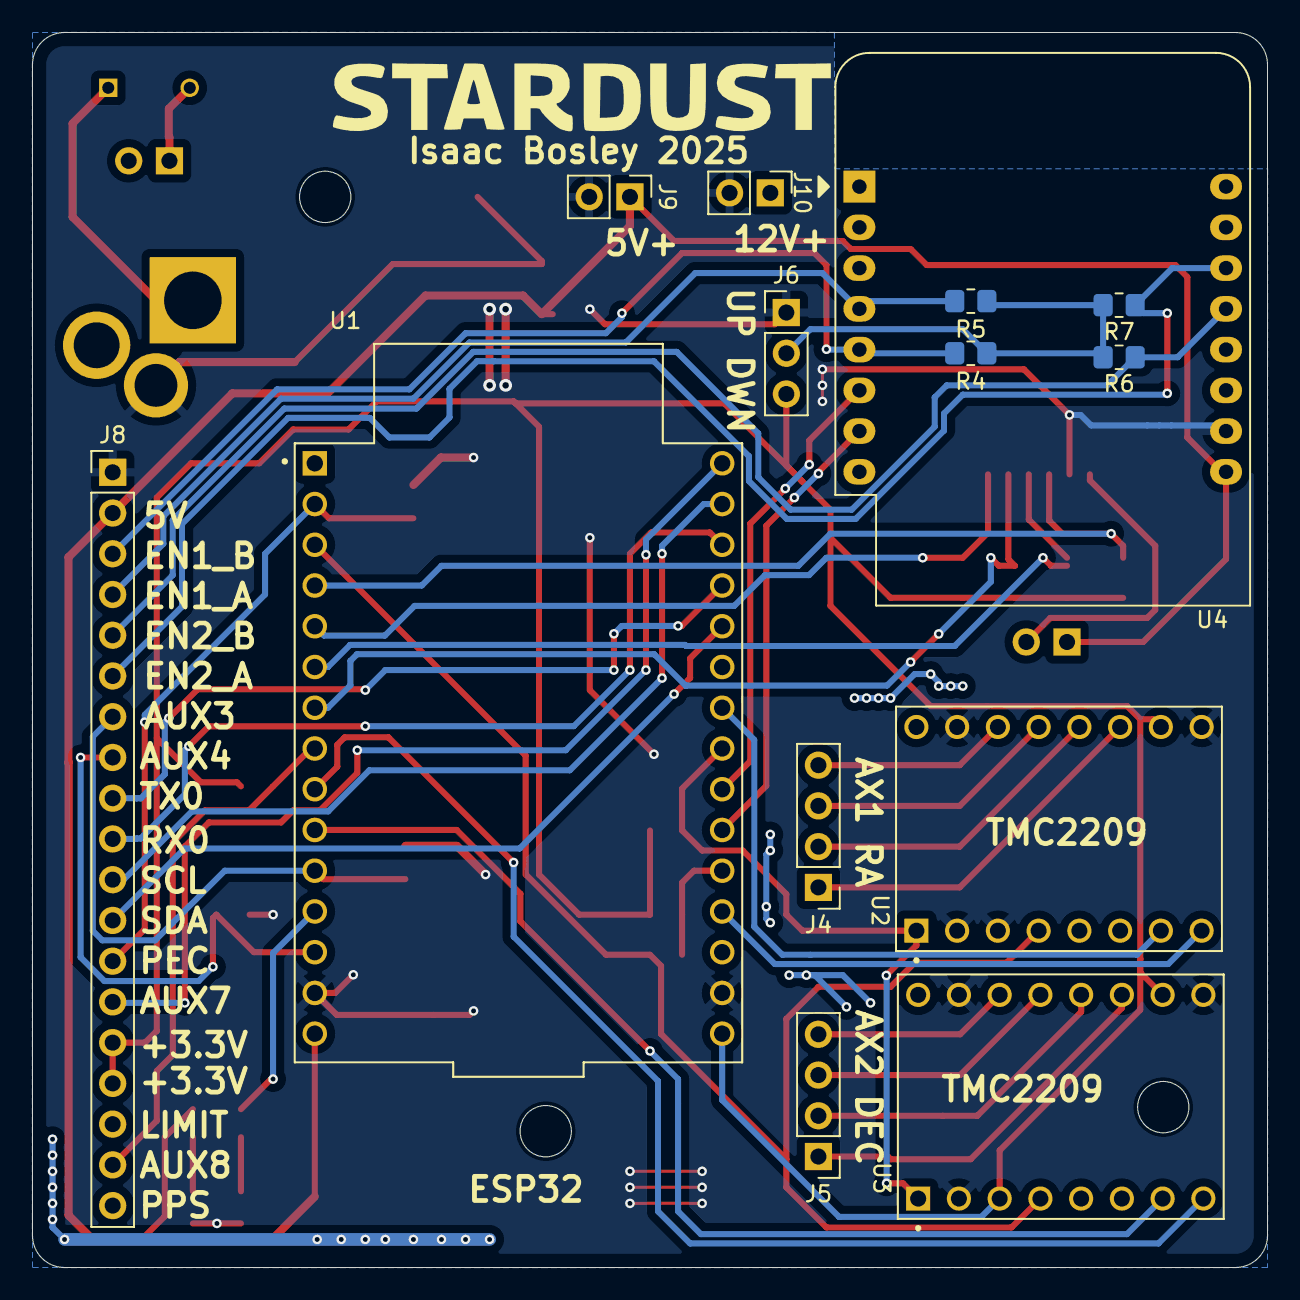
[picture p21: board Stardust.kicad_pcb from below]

Board: 2 copper layers, 77.0 x 77.0 mm, 42 parts (15 on the bottom side), 45 nets.

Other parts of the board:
G1#2: LOGO; logo_footprint

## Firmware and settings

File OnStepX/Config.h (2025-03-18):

/* ---------------------------------------------------------------------------------------------------------------------------------
 * Configuration for OnStepX
 *
 *          For more information on setting OnStep up see http://www.stellarjourney.com/index.php?r=site/equipment_onstep 
 *                      and join the OnStep Groups.io at https://groups.io/g/onstep
 * 
 *           *** Read the compiler warnings and errors, they are there to help guard against invalid configurations ***
 *
 * ---------------------------------------------------------------------------------------------------------------------------------
 * ADJUST THE FOLLOWING TO CONFIGURE YOUR CONTROLLER FEATURES ----------------------------------------------------------------------
 * <-Req'd = always must set, <-Often = usually must set, Option = optional, Adjust = adjust as req'd, Infreq = infrequently changed
*/
//      Parameter Name              Value   Default  Notes                                                                      Hint

// =================================================================================================================================
// CONTROLLER ======================================================================================================================
#define HOST_NAME                "OnStep" // nStep", Hostname for this device up to 16 chars.                                 Adjust

// PINMAP ------------------------------------------------- see https://onstep.groups.io/g/main/wiki/Configuration_Controller#PINMAP
#define PINMAP                        MaxESP4 //    OFF, Choose from: MiniPCB, MiniPCB2, MaxPCB4, MaxESP4, MaxSTM3, FYSETC_E4,   <-Req'd
                                          //         BTT_SKR_PRO, etc.  Other boards and more info. in ~/src/Constants.h                                   

// SERIAL PORT COMMAND CHANNELS --------------------- see https://onstep.groups.io/g/main/wiki/Configuration_Controller#SERIAL_PORTS
#define SERIAL_A_BAUD_DEFAULT        9600 //   9600, n. Where n=9600,19200,57600,115200,230400,460800 (common baud rates.)    Infreq
#define SERIAL_B_BAUD_DEFAULT        9600 //   9600, n. Baud rate as above. See (src/pinmaps/) for Serial port assignments.   Infreq
#define SERIAL_B_ESP_FLASHING         OFF //    OFF, ON Upload ESP8266 WiFi firmware through SERIAL_B with :ESPFLASH# cmd.    Option
#define SERIAL_C_BAUD_DEFAULT         OFF //    OFF, n. Baud rate as above. See (src/pinmaps/) for Serial port assignments.   Infreq
#define SERIAL_D_BAUD_DEFAULT         OFF //    OFF, n. Baud rate as above. See (src/pinmaps/) for Serial port assignments.   Infreq
#define SERIAL_E_BAUD_DEFAULT         OFF //    OFF, n. Baud rate as above. See (src/pinmaps/) for Serial port assignments.   Infreq
#define SERIAL_RADIO                  OFF //    OFF, Use BLUETOOTH or WIFI_ACCESS_POINT or WIFI_STATION (ESP32 only.)         Option

// STATUS --------------------------------------------- see https://onstep.groups.io/g/main/wiki/Configuration_Controller#STATUS_LED
#define STATUS_LED                    OFF //    OFF, Steady illumination if no error, blinks w/error code otherwise.          Option

// RETICLE CONTROL ------------------------------- see https://onstep.groups.io/g/main/wiki/Configuration_Controller#RETICLE_CONTROL
#define RETICLE_LED_DEFAULT           OFF //    OFF, n. Where n=0..255 (0..100%) activates feature sets default brightness.   Option
#define RETICLE_LED_MEMORY            OFF //    OFF, ON Remember reticle brightness across power cycles.                      Option
#define RETICLE_LED_INVERT            OFF //    OFF, ON Inverts control for cases where 0V is max brightness.                 Option

// WEATHER SENSOR --------------------------------- see https://onstep.groups.io/g/main/wiki/Configuration_Controller#WEATHER_SENSOR
#define WEATHER                       OFF //    OFF, BME280 (I2C 0x77,) BME280_0x76, BME280_SPI (see pinmap for CS.)          Option
                                          //         BMP280 (I2C 0x77,) BMP280_0x76, BMP280_SPI (see pinmap for CS.)
                                          //         BME280 or BMP280 for temperature, pressure.  BME280 for humidity also.

// SIGNALING ------------------------------------------- see https://onstep.groups.io/g/main/wiki/Configuration_Controller#SIGNALING
#define STEP_WAVE_FORM             SQUARE // SQUARE, PULSE Step signal wave form faster rates. SQUARE best signal integrity.  Adjust
                                          //         Applies to all axes.

// NON-VOLATILE MEMORY ---------------------------------------- see https://onstep.groups.io/g/main/wiki/Configuration_Controller#NV
#define NV_DRIVER              NV_DEFAULT // NV_DEF, Use platforms default non-volatile device to remember runtime settings.  Option
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

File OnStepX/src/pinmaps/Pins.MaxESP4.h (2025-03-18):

// -------------------------------------------------------------------------------------------------
// Pin map for OnStep MaxESP4 (ESP32S)
#pragma once

#if defined(ESP32)

// Serial0: RX Pin GPIO3, TX Pin GPIO1 (to USB serial adapter)
// Serial1: RX1 Pin GPIO10, TX1 Pin GPIO9 (on SPI Flash pins, must be moved to be used)
// Serial2: RX2 Pin GPIO16, TX2 Pin GPIO17

#if SERIAL_A_BAUD_DEFAULT != OFF
  #define SERIAL_A              Serial
#endif
#if SERIAL_B_BAUD_DEFAULT != OFF
  #define SERIAL_B              Serial2
#endif

// Use the following settings for any TMC UART driver (TMC2209) that may be present
#if defined(STEP_DIR_TMC_UART_PRESENT) || defined(SERVO_TMC2209_PRESENT)
  #define SERIAL_TMC_HARDWARE_UART
  #define SERIAL_TMC            Serial1          // Use a single hardware serial port to up to four drivers
  #define SERIAL_TMC_BAUD       460800           // Baud rate
  #define SERIAL_TMC_RX         39               // Recieving data
  #define SERIAL_TMC_TX         4                // Transmit data
  #define SERIAL_TMC_ADDRESS_MAP(x) ((x==1)?2 : x) // Axis1(0) is 0, Axis2(1) is 1, Axis3(2) is 2, Axis4(3) is 3, Axis5(4) is 2
#endif

// Specify the ESP32 I2C pins
#define I2C_SDA_PIN             21
#define I2C_SCL_PIN             22

// The multi-purpose pins (Aux3..Aux8 can be analog pwm/dac if supported)
#define AUX2_PIN                39               // M3 pin TMC UART RX
#define AUX3_PIN                14               // Home SW for Axis1
#define AUX4_PIN                13               // Home SW for Axis2
#define AUX5_PIN                1                // TX0 main USB, etc.
#define AUX6_PIN                3                // RX0 main USB, etc.
#define AUX7_PIN                23               // Limit SW, PPS, etc.
#define AUX8_PIN                25               // 1-Wire, Status LED, Reticle LED, Tone, etc.

// Misc. pins
#ifndef ONE_WIRE_PIN
  #define ONE_WIRE_PIN          AUX8_PIN         // Default Pin for OneWire bus
#endif

// The PEC index sense is a logic level input, resets the PEC index on rising edge then waits for 60 seconds before allowing another reset
#ifndef PEC_SENSE_PIN
  #define PEC_SENSE_PIN         36               // [input only 36] PEC Sense, analog (A0) or digital (GPIO36)
#endif

// The status LED w/ 4.7k resistor in series to limit the current to the LED
#ifdef STATUS_LED_ON_STATE
  #undef STATUS_LED_ON_STATE
#endif
#define STATUS_LED_ON_STATE HIGH
#ifndef STATUS_LED_PIN
  #define STATUS_LED_PIN        12               // Default LED Anode (+)
#endif
#ifdef MOUNT_LED_ON_STATE
  #undef MOUNT_LED_ON_STATE
#endif
#define MOUNT_LED_ON_STATE      HIGH
#define MOUNT_LED_PIN           STATUS_LED_PIN   // Default LED Anode (+)
#ifndef RETICLE_LED_PIN
  #define RETICLE_LED_PIN       AUX8_PIN         // Default LED Cathode (-)
#endif

// For a piezo buzzer
#ifndef STATUS_BUZZER_PIN
  #define STATUS_BUZZER_PIN     12               // [must be low at boot 12] Tone
#endif

// The PPS pin is a 3.3V logic input, OnStep measures time between rising edges and adjusts the internal sidereal clock frequency
#ifndef PPS_SENSE_PIN
  #define PPS_SENSE_PIN         AUX7_PIN         // PPS time source, GPS for example
#endif

// The limit switch sense is a logic level input normally pull high (2k resistor,) shorted to ground it stops gotos/tracking
#ifndef LIMIT_SENSE_PIN
  #define LIMIT_SENSE_PIN       AUX7_PIN
#endif

#define SHARED_DIRECTION_PINS                    // Hint that the direction pins are shared
#define SHARED_ENABLE_PIN       5                // Hint that the enable pins are shared

// Axis1 RA/Azm step/dir driver
#define AXIS1_ENABLE_PIN        SHARED           // Enable pin control
#define AXIS1_M0_PIN            OFF              // hardwired for TMC UART address 0
#define AXIS1_M1_PIN            OFF              // hardwired for TMC UART address 0
#define AXIS1_M2_PIN            OFF              // UART TX
#define AXIS1_M3_PIN            OFF              // UART RX
#define AXIS1_STEP_PIN          18
#define AXIS1_DIR_PIN           2                // [must be high at boot 0]
#ifndef AXIS1_SENSE_HOME_PIN
  #define AXIS1_SENSE_HOME_PIN  AUX3_PIN
#endif

// Axis2 Dec/Alt step/dir driver
#define AXIS2_ENABLE_PIN        SHARED
#define AXIS2_M0_PIN            OFF              // hardwired for TMC UART address 1
#define AXIS2_M1_PIN            OFF              // hardwired for TMC UART address 1
#define AXIS2_M2_PIN            OFF              // N/C
#define AXIS2_M3_PIN            OFF              // UART RX
#define AXIS2_STEP_PIN          27
#define AXIS2_DIR_PIN           26
#ifndef AXIS2_SENSE_HOME_PIN
  #define AXIS2_SENSE_HOME_PIN  AUX4_PIN
#endif
#ifndef AXIS2_ENCODER_B_PIN
  #define AXIS2_ENCODER_B_PIN   AUX2_PIN
#endif
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

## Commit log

2024-03-21 Added tangent and dovetail models made by JZ (Alkaid)
    [Dovetail_asm.SLDASM, alt_bolt_housing.SLDPRT, alt_locker_base.SLDPRT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]
2024-03-21 Revised both axis mounts to be smaller and more sleek looking. Also decided on using M3 to mount entire thing together (may upsize later)
    [STARDUST_ANGLEDBRACKED.SLDPRT, STARDUST_DEC_HARMONICMOUNT_V2.SLDPRT, STARDUST_RA_HARMONICMOUNT_V2.SLDPRT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]
2024-03-21 Added blanks for top and computer panels as well as an expense tracker and hours tracker
    [Hours_Expenses.xlsx, STARDUST_COMPUTERMOUNT_V2.SLDPRT, STARDUST_DEC_HARMONICMOUNT_V2.SLDPRT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]
2024-03-21 Switched top and computer locations around. Also added a M12x1.75 tap hole for a counterweight on back.
    [STARDUST_COMPUTERMOUNT_V2.SLDPRT, STARDUST_COUNTERWEIGHT_MOUNT_V2.SLDPRT, STARDUST_TOP_V2.SLDPRT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]
2024-03-22 Begun work on stepper mounts and adding in gearing/shafts.
    [3684N12_Corrosion-Resistant HTD Timing Belt Pulley.SLDPRT, 3764N101_High-Strength Gt Timing Belt Pulley.SLDPRT, 3764N11_High-Strength Gt Timing Belt Pulley.SLD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]
2024-03-22 Added in correct models for gears and mated everything accordingly.
    [GPA18GT2060-A-H5_b.sldprt, GPA60GT2060-A-H8_b.sldprt, GPA60GT2060-B-H8_b.sldprt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]
2024-03-22 Changed material to 6061 alum alloy. Cleaned up construction lines.
    [STARDUST_DEC_STEPPERMOUNT_WALL_V2.SLDPRT, STARDUST_RA_STEPPERMOUNT_WALL_V2.SLDPRT, STARDUST_STEPPER_BRACKET_V2.SLDPRT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]
2024-03-28 Updated hours
    [Hours_Expenses.xlsx]
2024-04-02 Updated Excel sheet
    [Hours_Expenses.xlsx]
2024-04-09 Added a electronics mount plate and changes some materials and colors. Also added a HD cover for looks and eventually addding the prox sensor and metal piece.
    [STARDUST_COMPUTERMOUNT_V2.SLDPRT, STARDUST_DEC_HDCOVER.SLDPRT, STARDUST_ELECTRONICS_MOUNT.SLDPRT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]
2024-09-04 Added .step file for easy viewing of asm
    The .step contains the tangent assembly from Alkaid mount as well as a dovetail from the same project. The final Stardust design will NOT include these models.
2024-11-13 Added nut holes for better bolting
    [Dovetail_asm.SLDASM, GPA18GT2060-A-H5_b.sldprt, GPA60GT2060-A-H8_b.sldprt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]
2025-02-18 Added Kicad stuff and updates some of the models.
    [12VREG_DPAK-3_ONS.step, 5188 DS3231 RTC.step, 5VREG_TS1117BCW50_RPG.stp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]
2025-02-18 More work on sch and board layout
    [RJ12_85513-5002.stp, Stardust.kicad_pcb, Stardust.kicad_sch]
2025-02-19 Finished schematic (V1.0)
    [12VREG_TO-252-3-L1_NMD.step, Stardust.kicad_pcb, Stardust.kicad_sch]
2025-02-19 Added parts for everything as well as assigned footprints. Board should be ready to finish
    [100uFElectrolyticCap_GXC1V101MCQ1GS.stp, 10uFElectrolyticCap_865230643009.stp, Stardust.kicad_pcb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]
2025-02-20 Finished board design and created gerber files
    [Stardust-B_Cu.gbr, Stardust-B_Mask.gbr, Stardust-B_Paste.gbr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]
2025-02-20 Added silkscreen images
    [Stardust-B_Cu.gbr, Stardust-B_Mask.gbr, Stardust-B_Paste.gbr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]
2025-02-20 Added 3d model of full board and a bom
    [bom.csv]
2025-02-20 Added bom and replaced expensive cap
    [Stardust-B_Cu.gbr, Stardust-B_Mask.gbr, Stardust-B_Paste.gbr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]
2025-02-20 updated bom and cleanup
    [bom.xlsx]
2025-02-20 Fixed some power plane issues and added mounting holes
    [Stardust-B_Cu.gbr, Stardust-B_Mask.gbr, Stardust-B_Paste.gbr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]
2025-03-02 Added software libraries for onstep as well as the configured code required to upload to esp32. Also included some Arduino libraries
    [Stardust-B_Cu.gbr, Stardust-B_Mask.gbr, Stardust-B_Paste.gbr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]
2025-03-05 Started revising board. Did stepper drivers and updated some footprints
    [Stardust.kicad_pcb, Stardust.kicad_sch]
2025-03-18 updated 3d model. Added new model parts. Updated board and firmware. Everything should be working in this rev
    [GPA18GT2060-A-H5_b.sldprt, GPA60GT2060-A-H8_b.sldprt, STARDUST_COMPUTERMOUNT_V2.3MF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]
2025-03-18 worked on computer mount model and cover
    [STARDUST_COMPUTERMOUNT_PART2_V2.3MF, STARDUST_COMPUTERMOUNT_PART2_V2.SLDPRT, STARDUST_COMPUTERMOUNT_V2.3MF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]
